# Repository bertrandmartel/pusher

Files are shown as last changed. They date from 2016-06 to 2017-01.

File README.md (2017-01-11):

# Pusher

 

Mechanical wall switch button pusher securely controlled via Bluetooth LE with RFduino module/LCD panel & via Android smartphone

Download Pusher from Google Play (https://play.google.com/store/apps/details?id=com.github.akinaru.roboticbuttonpusher)

demo

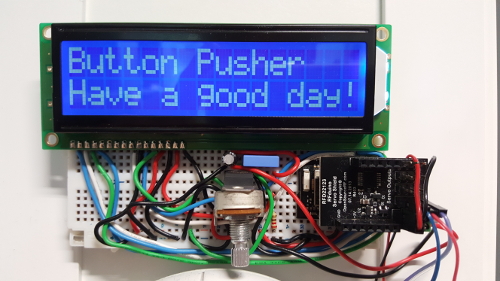
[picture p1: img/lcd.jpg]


***

Application layer association security  :

* AES 256 encryption
* user code for key exchange
* additional password protection

protected against MIM & Replay attack

pairing

## Project structure

* **/firmware** - microcontroller code written for RFduino
* **/android** - android application to control device
* **/hardware** - wiring diagram, schematics & BOM

## Build

### Get source code

```
git clone git@github.com:bertrandmartel/pusher.git
cd pusher
git submodule update --init --recursive
```

### Build Firmware

```
cd firmware
make
```

### Build Android App

```
cd android
./gradlew build
```

## [Firmware specifications](https://github.com/bertrandmartel/pusher/blob/master/firmware/README.md)

## [Hardware specifications](https://github.com/bertrandmartel/pusher/blob/master/hardware/README.md)

## External library

### Firmware

* rfduino software : https://github.com/RFduino/RFduino
* LiquidCrystal arduino library : https://github.com/arduino-libraries/LiquidCrystal
* rfduino-makefile : https://github.com/bertrandmartel/rfduino-makefile
* AES library by Brian Gladman

### Android application

* smart Android dot progress bar : https://github.com/silvestrpredko/DotProgressBarExample
* AES library by Brian Gladman
* appcompat-v7, design & recyclerview-v7

## License

```
Copyright (C) 2016  Bertrand Martel

This program is free software; you can redistribute it and/or
modify it under the terms of the GNU General Public License
as published by the Free Software Foundation; either version 3
of the License, or (at your option) any later version.

Pusher is distributed in the hope that it will be useful,
but WITHOUT ANY WARRANTY; without even the implied warranty of
MERCHANTABILITY or FITNESS FOR A PARTICULAR PURPOSE.  See the
GNU General Public License for more details.

You should have received a copy of the GNU General Public License
along with Pusher.  If not, see <http://www.gnu.org/licenses/>.
```

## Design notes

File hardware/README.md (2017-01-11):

## Hardware Specifications

Button pusher device is composed of :
* a mechanical part : servomotor + bracket + support
* an hardware part : rfduino uc + servo shield + LCD panel + voltage regulator

Check [Bill of Materials file](./BOM.xls) for a concise list of all hardware elements used in that project & links to some providers

### Hardware Parts

* [RFduino uc module](http://www.rfduino.com/product/rfd22102-rfduino-dip/index.html)

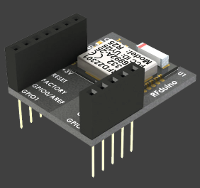
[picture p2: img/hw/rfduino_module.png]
rfduino


* [RFduino servo module](http://www.rfduino.com/product/rfd22123-servo-shield-for-rfduino/index.html)

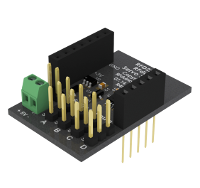
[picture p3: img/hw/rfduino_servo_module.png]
rfduino


* [3V3 NewHaven LCD panel](http://www.mouser.fr/Search/ProductDetail.aspx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)

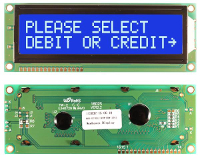
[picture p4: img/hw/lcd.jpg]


* [5V to 3V3 Voltage regulator LD1117V33](http://www.mouser.fr/ProductDetail/STMicroelectronics/LD1117V33/?qs=sGAEpiMZZMvHdo5hUx%252bJYl1lUmOd3DGr)

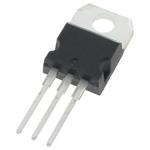
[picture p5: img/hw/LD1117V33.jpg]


* [Rfduino UART module](http://www.rfduino.com/product/rfd22121-usb-shield-for-rfduino/index.html) (for uploading/debgging purpose)

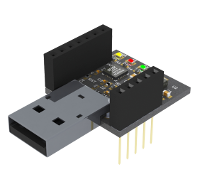
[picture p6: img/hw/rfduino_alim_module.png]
rfduino


### Prototype wiring 

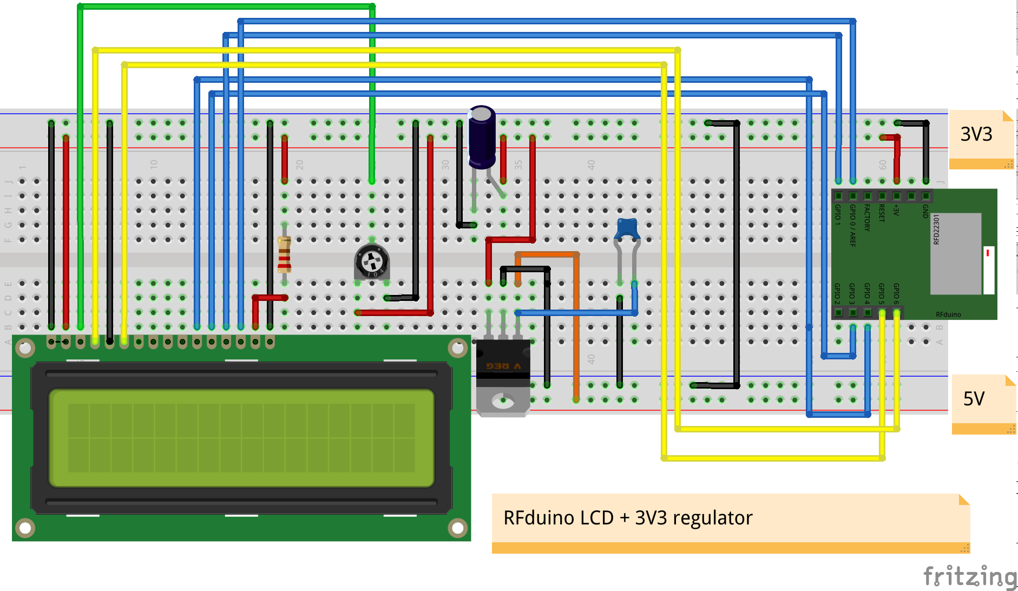
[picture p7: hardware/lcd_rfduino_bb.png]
wiring


### Mechanical Parts

This device is meant to push a wall switch of "Mosaic" type which is harder to push than a regular wall switch. To have enough force to push it, a servomotor with High Torque is used. HS-625MG is good for this task with a torque of 5.5 / 6.8 kg (http://www.imagesco.com/servo/motors/HS-625MG.html).

An aluminium sheet is used to support this servomotor : 

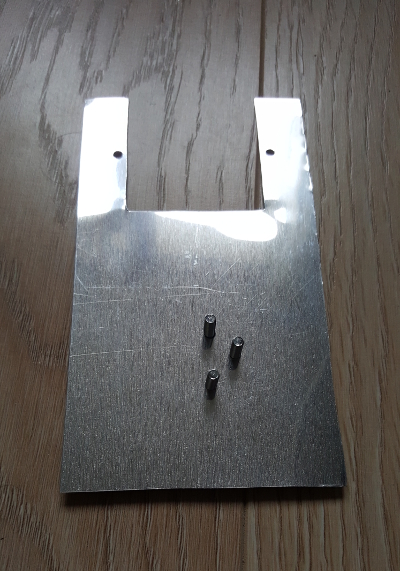
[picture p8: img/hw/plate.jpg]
aluminium_sheet


Servomotor is fixed to the bracket, the bracket is fixed to this plate :

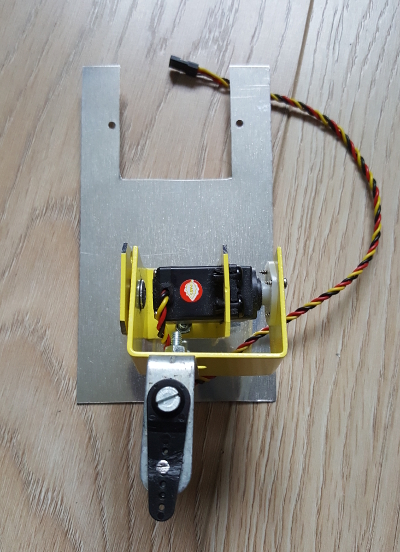
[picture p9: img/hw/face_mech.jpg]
bracket_servo


You can use 3.5mm or 4.mm screws with imagesco bracket (http://www.imagesco.com/catalog/servobot/SUB-01.pdf) :

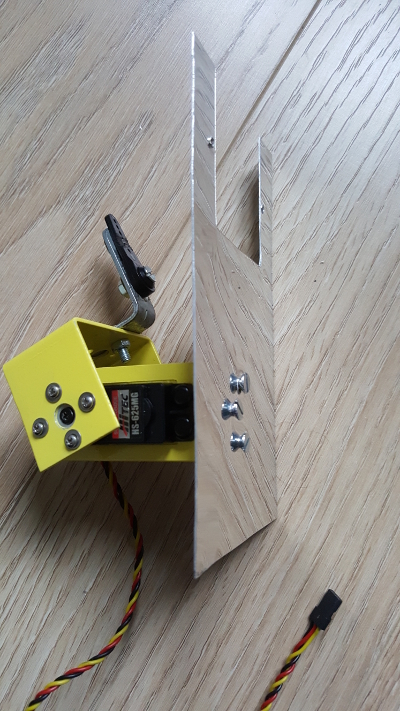
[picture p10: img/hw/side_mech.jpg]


The servomotor is then connected to Rfduino servo shield module that features an external 5V DC supply :

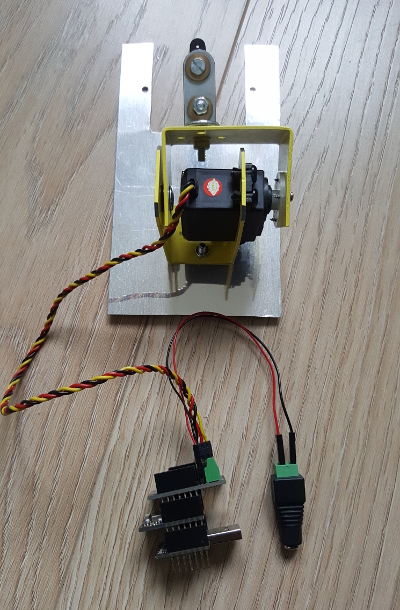
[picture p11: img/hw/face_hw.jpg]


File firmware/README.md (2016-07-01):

## Firmware Specifications

This wall switch pusher offers following features :
* push function
* LCD panel message
* secure association between Android smartphone & device via LCD panel
* persistent storage on the device to store associated device, security secrets such as key/iv, LCD panel message to be displayed
* all functionnalities except association are password protected

## Security features

This device uses AES 256 bit encyption based on the implementation by Brian Gladman (it used 8-bit byte operation only). The same implementation is used on both side, on Android & on RFduino uc.

Each smartphone Bluetooth controller will associate with the device generating a unique couple xor-key / serial number. This information is sent to the RFduino device and stored in persistent storage. The device will send back its AES key/iv. The whole association is protected by an AES key/iv generated from a random key the user must type on Android smartphone & generated by RFduino device. As a consequence, to associate with Rfduino device, a human must reproduce a visual information via the LCD panel.

All APIs are protected by a one-shot token generated by RFduino device. A GET_TOKEN API is used to retrieve this token from RFduino device. This token is encoded with Smartphone unique xor-key & AES encryption. This assure no replay attack is possible.

The critical APIs are secured by an additionnal password which must be changed when you setup the device for the first time. Default password is "admin". This password is encoded with the smartphone xor-key & encypted with AES.

## API parameters

* abbreviation
 * SN : serial number
 * pwd : password
 * token : random string (can be used only once)
 * AES : encyption with AES key stored on RFduino device
 * AES2 : encyption with AES key generated from user visual code (shared with user via LCD panel)
 * XOR : xor encryption with a xor-key user-specific (generated & exchanged at association)

|  name | code | input params |  output params  | LCD code |
|---|---|---|---|---|
| GET_TOKEN | 0x00 |  - | [token] |  no |
| ASSOCIATION_STATUS | 0x01 |  AES(SN + XOR([token])) | [status code] |  no |
| PUSH | 0x02 |  AES(SN + XOR(pwd + [token]))  | [status code] |  no |
| SET_PASSWORD | 0x03 |  AES(SN + XOR(pwd + [token]))  | [status code] |  yes | 
| ASSOCIATE | 0x04 |  - | [status code] |  yes | 
| SET_KEYS | 0x05 |  AES(SN + XOR(pwd + [token]))  | [status code] |  yes | 
| FAILURE | 0x06 |  - | - |  no | 
| ASSOCIATE_RESPONSE | 0x07 |  AES2(SN + XOR(pwd + [token])) | [status code] |  no | 
| RECEIVE_KEYS | 0x08 |  - | [status code] |  no | 
| SET_PASSWORD_RESPONSE | 0x09 |  AES2(SN + XOR(pwd + [token])) | [status code] |  no | 
| SET_KEYS_RESPONSE | 0x0A |  AES2(SN + XOR(pwd + [token])) | [status code] |  no | 
| DEASSOCIATE | 0x0B |  AES(SN + XOR(pwd + [token])) | [status code] |  no | 
| MESSAGE_TOP | 0x0C |  AES(SN + XOR(pwd + [token])) | [status code] |  no | 
| MESSAGE_BOTTOM | 0x0D |  AES(SN + XOR(pwd + [token])) | [status code] |  no |

## API description

|  name | description |
|---|---|
| GET_TOKEN |  get a token that can be used only once |
| ASSOCIATION_STATUS |  ask the device if the SN/XOR key pair sent is already associated |
| PUSH |  push wall switch |
| SET_PASSWORD |  change the password on the RFduino device, this will trigger a user code displayed on LCD |
| ASSOCIATE |  trigger association for the SN/XOR key pair sent, this will trigger a user code displayed on LCD |
| SET_KEYS |  change the AES key/iv on the RFduino device, this will trigger a user code displayed on LCD |
| FAILURE |  send a failure command |
| ASSOCIATE_RESPONSE |  send the association request encoded with the new AES2 key generated from user code |
| RECEIVE_KEYS |  request the keys from the RFduino device. This will only return keys if the association was performed just before |
| SET_PASSWORD_RESPONSE |  send the change-password request encoded with the new AES2 key generated from user code |
| SET_KEYS_RESPONSE |  send the change-keys request encoded with the new AES2 key generated from user code |
| DEASSOCIATE |  disassociate the SN/Xor key pair (delete from persistent storage as well) |
| MESSAGE_TOP |  change the top default message of the LCD screen |
| MESSAGE_BOTTOM |  change the bottom default message of the LCD screen |

## GATT protocol

* the above commands/APIs are sent via GATT characteristic `00002222-0000-1000-8000-00805f9b34fb`
* result is received via GATT characteristic `00002221-0000-1000-8000-00805f9b34fb` via notification

## Large data via GATT protocol

* The limit for GATT characteristic payload is 18 octet. The above commands load more than 18 octet, so payload is divided in bunch of 18 octet sent separatly. The first frame sent to Rfduino device is a frame containing the command code and the length of the payload. When the total payload is received from the device, it is processed directly and the response is returned via notification on characteristic `00002221-0000-1000-8000-00805f9b34fb`.

* The same protocol is used for receiving data from the Rfduino device. Data is split into bunch of 18 octet and sent until everything is received.

## Persistent storage

### Device configuration

Device configuration features a list of `device` structure featuring : 

| prototype | description |
|---|---|
| char device_id[8]  |  device serial |
| char xor_key[32] |  XOR key |

The maximum associated device number is 25 device (page size is 1024 octet)

### Global configuration

Global configuration features :

| prototype | description |
|---|---|
| char pass[4*16] |  encrypted password |
| uint16_t flag |  flag to check against default configuration |
| uint8_t device_num |  device_num for the number of smartphone device associated |
| char key[32] |  AES key |
| char iv[16] |  AES iv  |
| char top_message[28] | LCD panel top default message |
| char bottom_message[28] | LCD panel bottom default message |

### Memory page

* smartphone devices configuration is stored on page 250
* global configuration is stored on page 251

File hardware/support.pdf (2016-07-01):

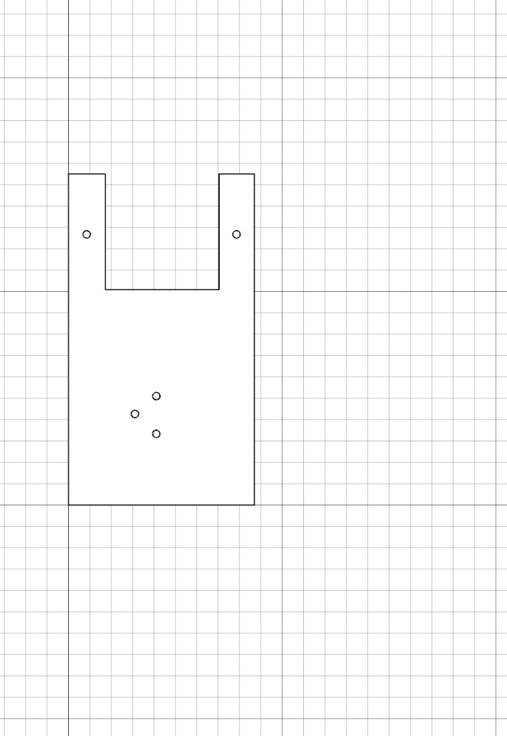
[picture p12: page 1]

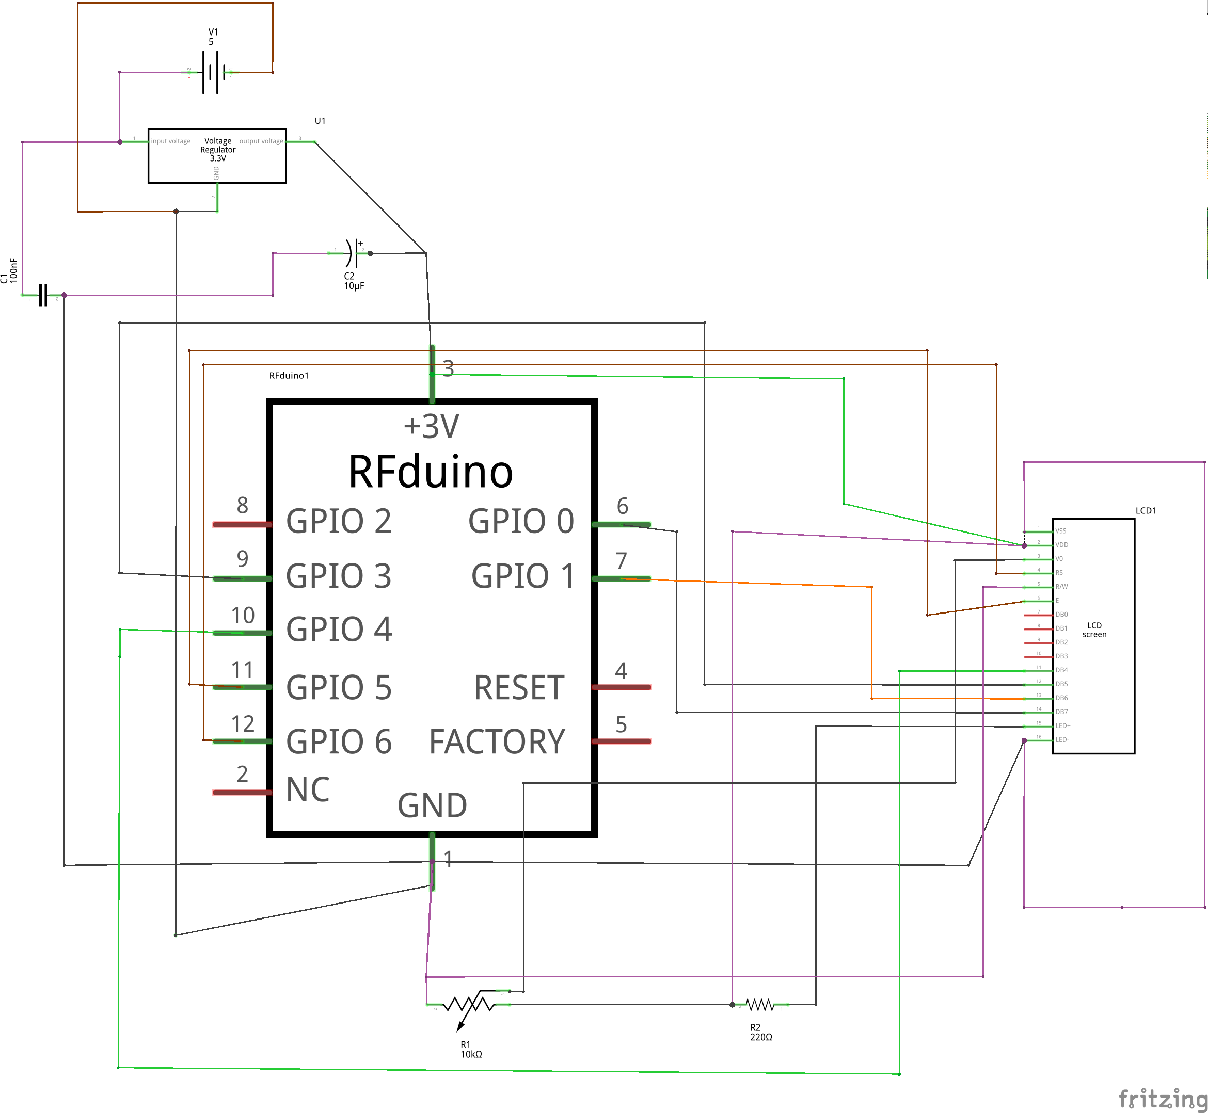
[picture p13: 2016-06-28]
hardware/lcd_rfduino_schem.png

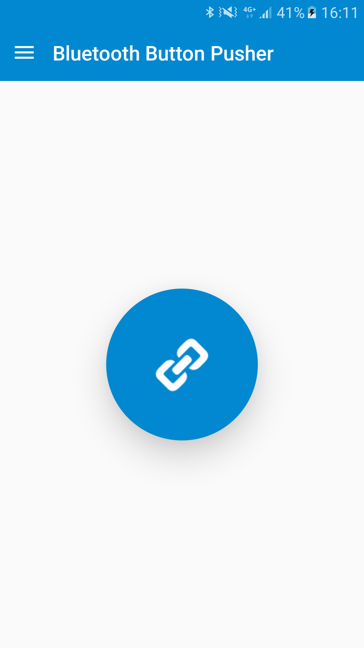
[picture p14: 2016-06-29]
img/screenshot1.png

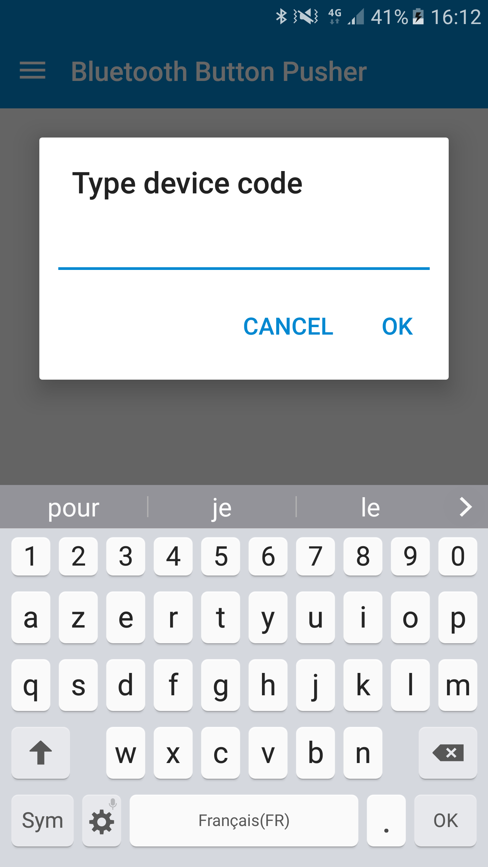
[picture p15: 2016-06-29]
img/screenshot2.png

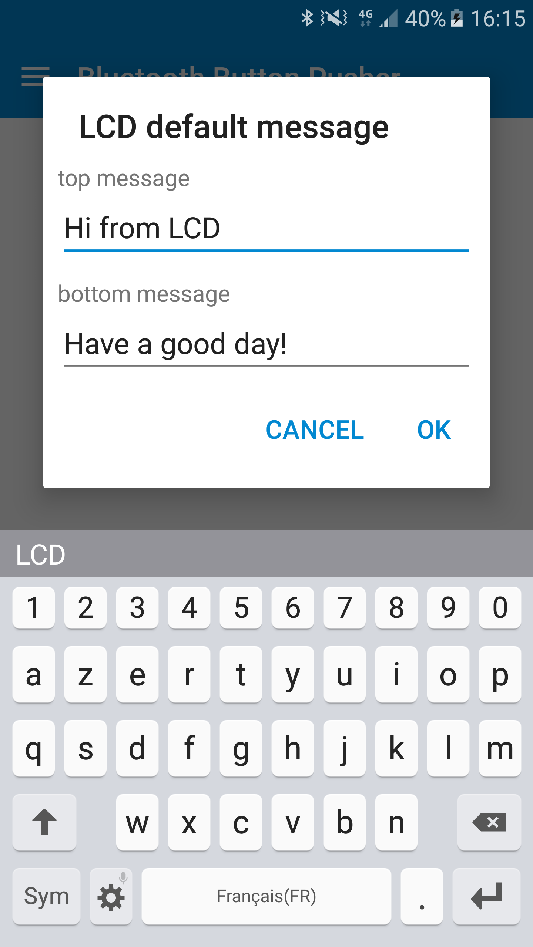
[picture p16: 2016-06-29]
img/screenshot6.png

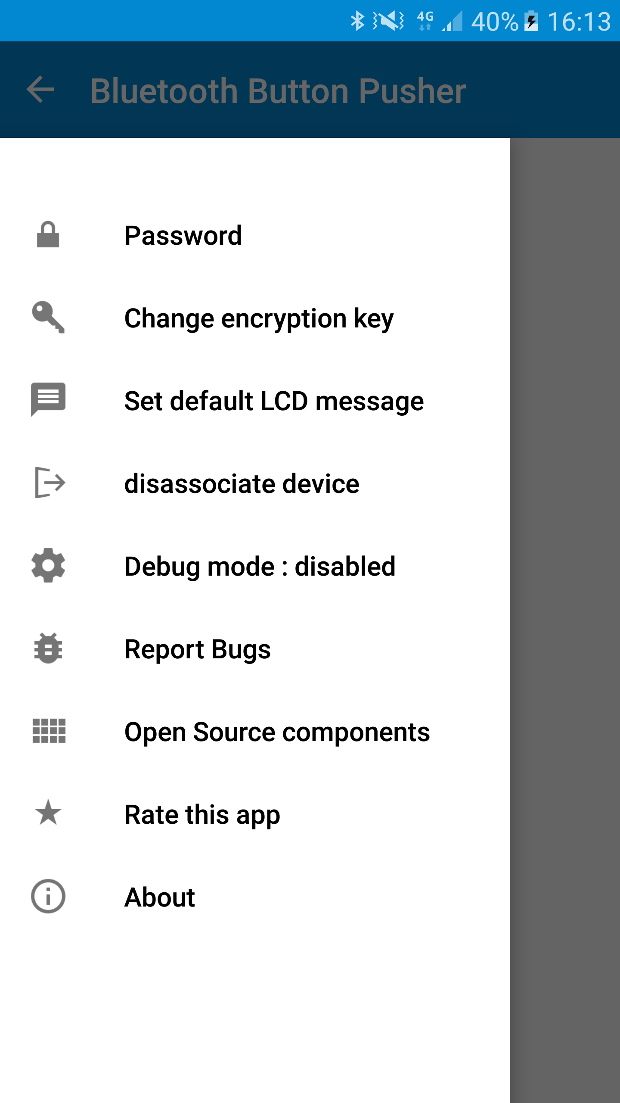
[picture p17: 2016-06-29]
img/screenshot3.png

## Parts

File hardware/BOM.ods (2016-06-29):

Mechanical Specifications
brand | model name | title | description | link | quantity | Price in $ (06/2016)
imagesco | SUB-01 | servomotor bracket | bracket used to initiate translation movement | http://www.imagesco.com/catalog/servobot/SUB-01.pdf | 1 | $12.50
 |  | aluminium sheet | sheet to be drilled to maintain the device with wall switch screws | http://www.castorama.fr/store/Tole-alu-brut-prod7220028.html | 1 | $7.58
 |  | screws 40mm diameter | to fix servomotor to aluminium sheet & servo arms to metal corner brace |  | 6
 |  | nuts 40mm | to fix servomotor to aluminium sheet & servo arms to metal corner brace |  | 5
 |  | washer 40mm | to fix servomotor to aluminium sheet & servo arms to metal corner brace |  | 6
Hitech | HS-625MG | servomotor | the servomotor to be chosen with high torque | http://www.imagesco.com/servo/motors/HS-625MG.html | 1 | $39.95
Hitech |  | Super-Duty Arms | small arms used to press the button from the metal corner : to prevent roughening wall switch surface | https://www.servocity.com/html/hitec_super-duty_horns.html#.V3PHmHV97CI | 1 | $10.95
 |  | Metal Corner Brace Angle Bracket Fasteners | mounting fixed to servo bracket used to press button | http://fr.aliexpress.com/item/1-3-5-x-1-3-5-Metal-Corner-Brace-Angle-Bracket-Fasteners-5-Pcs/32382146337.html | 1 | $5.67
Hardware Specifications
brand | model name | title | description | link | quantity | Price in $ (06/2016)
rfduino | RFD22102 | Rfduino DIP | Chip embedding cortex M0 + nRF81522 | http://eu.mouser.com/ProductDetail/RF-Digital-Wireless/RFD22102/ | 1 | $28.99
rfduino | RFD22121 | USB Shield for Rfduino | rfduino shield used to load code | http://www.mouser.fr/ProductDetail/RF-Digital/RFD22121/ | 1 | $28.99
rfduino | RFD22123 | Servo Shield for Rfduino | rfduino shield used to control up to 4 servomotors | http://www.mouser.fr/ProductDetail/RF-Digital/RFD22123/ | 1 | $18.94
 |  | switching power supply | power supply 5V 2A | https://www.adafruit.com/product/276 | 1 | $7.95
 |  | potentiometer 10K linear | potentiometer to control LCD contrast | https://www.adafruit.com/products/562 | 1 | $0.95
 |  | 220 ohm resistor | pull up resistor | https://www.adafruit.com/products/2780 | 1 | $0.75
 | LD1117V33 | voltage regulator | regulate 5V to 3.3V | https://www.adafruit.com/products/2165 | 1 | $1.25
 |  | capacitor 10uf | Protect capacitor for Vout | https://www.adafruit.com/products/2195 | 1 | $1.95
 |  | capacitor 100nf | Protect capacitor for Vin | https://www.adafruit.com/products/2195 | 1
 |  | DC jack converter | Female DC Power adapter - 2.1mm jack to screw terminal block | https://www.adafruit.com/products/368 | 1 | $2.00
 |  | LCD character display | 3.3V character display LCD | http://www.mouser.fr/Search/ProductDetail.aspx | 1 | $21.95
total estimated price for prototype |  | $190.37

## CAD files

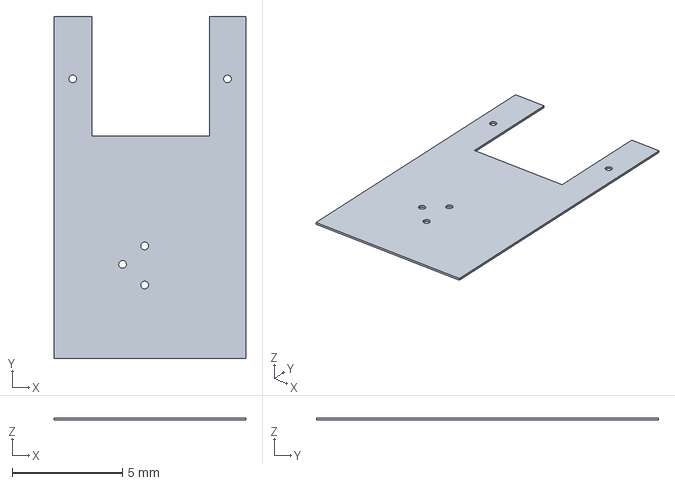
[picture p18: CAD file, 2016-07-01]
hardware/support.fcstd
8.70 x 15.5 x 0.1 mm

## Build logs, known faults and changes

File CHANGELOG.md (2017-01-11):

# Change Log

## [1.3](https://github.com/bertrandmartel/pusher/tree/1.3) (2016-07-05)
[Full Changelog](https://github.com/bertrandmartel/pusher/compare/1.2...1.3)

## [1.2](https://github.com/bertrandmartel/pusher/tree/1.2) (2016-07-01)
[Full Changelog](https://github.com/bertrandmartel/pusher/compare/1.1...1.2)

## [1.1](https://github.com/bertrandmartel/pusher/tree/1.1) (2016-07-01)
[Full Changelog](https://github.com/bertrandmartel/pusher/compare/1.0...1.1)

## [1.0](https://github.com/bertrandmartel/pusher/tree/1.0) (2016-06-29)

\* *This Change Log was automatically generated by [github_changelog_generator](https://github.com/skywinder/Github-Changelog-Generator)*

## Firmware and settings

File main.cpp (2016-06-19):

#include "Arduino.h"
#include <Servo.h>
#include <RFduinoBLE.h>
#include <string>
#include <LiquidCrystal.h>

#include <AES.h>

#define E(x,y) x = y,
enum STATE_ENUM {
#include "state.h"
};

#define E(x,y) #x,
static const char *STATE_STRING_ENUM[] = {
#include "state.h"
};

#define E(x,y) x = y,
enum COMMAND_ENUM {
#include "command.h"
};

#define E(x,y) #x,
static const char *COMMAND_STRING_ENUM[] = {
#include "command.h"
};

struct device
{
  char device_id[8];
  char xor_key[32];
};

#define LFSR_DEFAULT_VALUE 0xACE1u
#define MAX_ASSOCIATED_DEVICE 25
#define MESSAGE_DEFAULT "Have a good day!"
#define CODE_EXPIRING_TIME_SECONDS 30

device * device_ptr = new device[MAX_ASSOCIATED_DEVICE];
char token[16];

uint8_t state = STATE_NONE;
uint8_t state_count= 0;
uint8_t cmd = 0;
uint16_t data_length = 0;
bool use_local_keys = true;
uint16_t sending_index = 0;
bool code_expiring=false;
unsigned long code_expiring_time=0;

AES aes ;

byte default_key[32] = 
{
  0xF2, 0x1E, 0x07, 0x8C, 0x96, 0x99, 0x5E, 0xF7, 0xED, 0xF0, 0x91, 0x84, 0x06, 0x06, 0xF3, 0x94,
  0x59, 0x90, 0x66, 0x63, 0x81, 0xE9, 0x14, 0x3E, 0x7B, 0x02, 0x7E, 0x08, 0xB6, 0xC7, 0x06, 0x26
} ;

byte default_iv[16] = 
{
  0xC3, 0x78, 0x7E, 0x76, 0x31, 0x6D, 0x6B, 0x5B, 0xB8, 0x8E, 0xDA, 0x03, 0x82, 0xEB, 0x57, 0xBD
} ;

byte default_pass[64] = { 
  0x61, 0x64, 0x6d, 0x69, 0x6e, 0x00, 0x00, 0x00, 0x00, 0x00, 0x00, 0x00, 0x00, 0x00, 0x00, 0x00,
  0x00, 0x00, 0x00, 0x00, 0x00, 0x00, 0x00, 0x00, 0x00, 0x00, 0x00, 0x00, 0x00, 0x00, 0x00, 0x00,
  0x00, 0x00, 0x00, 0x00, 0x00, 0x00, 0x00, 0x00, 0x00, 0x00, 0x00, 0x00, 0x00, 0x00, 0x00, 0x00,
  0x00, 0x00, 0x00, 0x00, 0x00, 0x00, 0x00, 0x00, 0x00, 0x00, 0x00, 0x00, 0x00, 0x00, 0x00, 0x00,
};

byte external_key[32];
byte external_iv[16];

uint8_t* payload;
uint8_t* response;
uint8_t offset = 0;
uint16_t lfsr;

#define CONFIG_STORAGE 251
#define DEVICE_CONFIG_STORAGE 250

#define  str(x)   xstr(x)
#define  xstr(x)  #x

int interupt_pin = 31;

uint8_t myRandom8(){

  uint8_t __value;

  NRF_RNG->TASKS_START = 1; // Turn on the RNG.

  NRF_RNG->EVENTS_VALRDY = 0; // wait for a RNG value to be available

  while( NRF_RNG->EVENTS_VALRDY == 0 ){}
  __value = (uint8_t)NRF_RNG->VALUE; // read the RNG value

  NRF_RNG->TASKS_STOP = 1; // Turn off the RNG if we don't need it much.

  return(__value);
}

uint16_t myRandom16(){
  return(myRandom8() * myRandom8());
}

struct data_t
{
  char pass[4*N_BLOCK];
  uint16_t flag;
  uint8_t device_num;
  char key[32];
  char iv[16];
};

data_t config = { 
  "admin" ,
  0,
  0,
  {
  0xF2, 0x1E, 0x07, 0x8C, 0x96, 0x99, 0x5E, 0xF7, 0xED, 0xF0, 0x91, 0x84, 0x06, 0x06, 0xF3, 0x94,
  0x59, 0x90, 0x66, 0x63, 0x81, 0xE9, 0x14, 0x3E, 0x7B, 0x02, 0x7E, 0x08, 0xB6, 0xC7, 0x06, 0x26
},
  {
  0xC3, 0x78, 0x7E, 0x76, 0x31, 0x6D, 0x6B, 0x5B, 0xB8, 0x8E, 0xDA, 0x03, 0x82, 0xEB, 0x57, 0xBD
}
};

Servo s1;

bool add_device_pending = false;

data_t *in_flash = (data_t*)ADDRESS_OF_PAGE(CONFIG_STORAGE);

uint32_t *device_config = ADDRESS_OF_PAGE(DEVICE_CONFIG_STORAGE);

uint16_t bit;

LiquidCrystal lcd(6, 5, 4, 3, 1, 0);

uint16_t random()
{
  bit  = ((lfsr >> 0) ^ (lfsr >> 2) ^ (lfsr >> 3) ^ (lfsr >> 5) ) & 1;
  return lfsr =  (lfsr >> 1) | (bit << 15);
}

void write_host_config(device *item){

  int rc = flashWriteBlock(device_config, item, sizeof(device));
  device_config+=10;

    lcd.clear();
    lcd.print("write status : ");
    lcd.print(rc);
  
  #ifdef __PRINT_LOG__
    if (rc == 0){
      Serial.println("Success");
    }
    else if (rc == 1){
        Serial.println("Error - the flash page is reserved");
      }
    else if (rc == 2){
        Serial.println("Error - the flash page is used by the sketch");
      }
  #endif //__PRINT_LOG__
}

void save_config(bool default_config){

    #ifdef __PRINT_LOG__
      Serial.println("save_config");
    #endif //__PRINT_LOG__

    if (default_config){

      byte succ = aes.set_key (default_key, 256);

      int blocks = 4;
      byte cipher [4*N_BLOCK] ;
      byte iv [N_BLOCK];

      if (blocks == 1){
        succ = aes.encrypt(default_pass, cipher) ;
      }
      else {

        for (byte i = 0 ; i < N_BLOCK ; i++){
          iv[i] = default_iv[i] ;
        }
        succ = aes.cbc_encrypt(default_pass, cipher, blocks, iv) ;
      }

      for (byte i = 0; i < (4*N_BLOCK); i++){
        config.pass[i]=cipher[i];
      }

      #ifdef __PRINT_LOG__
        for (byte i = 0; i < (4*N_BLOCK); i++){
          Serial.print (cipher[i]>>4, HEX) ; Serial.print (cipher[i]&15, HEX) ; Serial.print (" ") ;
        }
        Serial.println();
      #endif //__PRINT_LOG__

      config.flag = 1;
      config.device_num=0;

      for (int i  =0;i< 32;i++){
        config.key[i]=default_key[i];
      }
      for (int i  =0;i< 16;i++){
        config.iv[i]=default_iv[i];
      }
    }
    
    while (!RFduinoBLE.radioActive);
    while (RFduinoBLE.radioActive);

    RFduinoBLE.end();

    flashPageErase(PAGE_FROM_ADDRESS(in_flash));

    while (RFduinoBLE_radioActive);

    flashWriteBlock(in_flash, &config, sizeof(config));

    if (add_device_pending){

      #ifdef __PRINT_LOG__
        Serial.println("in add_device_pending");
      #endif //__PRINT_LOG__

      if (config.device_num>0){

        #ifdef __PRINT_LOG__
          Serial.println("saving new associated device");
        #endif //__PRINT_LOG__

        write_host_config(&device_ptr[config.device_num-1]);
        //lcd.clear();
        //lcd.print("associated!");
      }
    }
}

void add_device(char * device_id,char * xor_key){

  #ifdef __PRINT_LOG__
    Serial.println("adding device in configuration");
  #endif //__PRINT_LOG__

  if (config.device_num<MAX_ASSOCIATED_DEVICE){

    #ifdef __PRINT_LOG__
      Serial.println(config.device_num);
    #endif //__PRINT_LOG__

    memcpy(device_ptr[config.device_num].device_id, device_id,8);
    memcpy(device_ptr[config.device_num].xor_key, xor_key,32);

    #ifdef __PRINT_LOG__
      Serial.println("add device to config");
    #endif //__PRINT_LOG__

    config.device_num++;

    add_device_pending=true;

    #ifdef __PRINT_LOG__
      Serial.println(config.device_num);
    #endif //__PRINT_LOG__

  }
  else{

    #ifdef __PRINT_LOG__
      Serial.println("error max device is reached");
    #endif //__PRINT_LOG__

  }
}

void load_fake_host_config(){

  for (int i = 0; i< MAX_ASSOCIATED_DEVICE;i++){

    if (i>=0){
      char buf[8];
      char xor_key[32];

      sprintf(buf, "d%d",i);
      sprintf(xor_key, "xor%d",i);

      strcpy(device_ptr[i].device_id, buf);
      strcpy(device_ptr[i].xor_key, xor_key);
    }
    else {
      char buf[8]={5, 21, 125, 245, 252, 14 ,86 ,59};
      char xor_key[32]={
        0x72, 0x6E , 0x35, 0x77, 0x6D, 0x64, 0x64, 0x64, 0x32, 0x62, 0x71, 0x31, 0x65, 0x64, 0x6B, 0x63, 0x62, 0x34, 0x68, 0x31, 0x76, 0x76, 0x73, 0x6B, 0x6F, 0x7A, 0x75, 0x71, 0x68, 0x33, 0x6A, 0x77
      };

      strcpy(device_ptr[i].device_id, buf);
      strcpy(device_ptr[i].xor_key, xor_key);
    }

    #ifdef __PRINT_LOG__
      Serial.print(i);
      Serial.print(" => ");
      Serial.print(device_ptr[i].device_id);
      Serial.print(" : ");
      Serial.println(device_ptr[i].xor_key);
    #endif //__PRINT_LOG__

  }
}

void print_all_config(){
  
  uint32_t *save_ptr = device_config;

  save_ptr = ADDRESS_OF_PAGE(DEVICE_CONFIG_STORAGE);

  device *item = 0;

  #ifdef __PRINT_LOG__
    Serial.println("-----------------------------");
    Serial.print("associated device list (size : ");
    Serial.print(config.device_num);
    Serial.println(") : ");
  #endif //__PRINT_LOG__
  
  for (int i = 0; i< config.device_num;i++){
    item = (device*)save_ptr;

    strcpy(device_ptr[i].device_id, item->device_id);
    strcpy(device_ptr[i].xor_key, item->xor_key);

    #ifdef __PRINT_LOG__
      for (int j = 0 ; j < 8;j++){
        Serial.print (device_ptr[i].device_id[j]>>4, HEX) ; Serial.print (device_ptr[i].device_id[j]&15, HEX) ; Serial.print (" ") ;
      }
      Serial.print(" | ");
      for (int j = 0 ; j < 32;j++){
        Serial.print (device_ptr[i].xor_key[j]>>4, HEX) ; Serial.print (device_ptr[i].xor_key[j]&15, HEX) ; Serial.print (" ") ;
      }
      Serial.println("");
    #endif //__PRINT_LOG__

    save_ptr+=10;
  }

  #ifdef __PRINT_LOG__
    Serial.println("-----------------------------");
  #endif //__PRINT_LOG__
}

void erase_host_config(){

  flashPageErase(PAGE_FROM_ADDRESS(device_config));

  for (int i = 0; i< MAX_ASSOCIATED_DEVICE;i++){
    strcpy(device_ptr[i].device_id, "");
    strcpy(device_ptr[i].xor_key, "");
  }
}

char* is_associated(char * device_id){

  Serial.println("in is_associated");
  for (int i  = 0; i  < 8;i++){
    char test[2];
    sprintf(test,"%02X",device_id[i]);
    Serial.print(test);
  }
  Serial.println("");

  for (int i = 0; i< MAX_ASSOCIATED_DEVICE;i++){

    if (memcmp(device_ptr[i].device_id,device_id,8)==0){
      return device_ptr[i].xor_key;
    }
  }
  return 0;
}

void remove_device(char * device_id){

  int index = 0;

  for (int i = 0; (i< MAX_ASSOCIATED_DEVICE);i++){

    if (memcmp(device_ptr[i].device_id,device_id,8)==0){
      index=i;
    }
  }
  if (index!=MAX_ASSOCIATED_DEVICE){
    for (int i = index;i<MAX_ASSOCIATED_DEVICE-1;i++){
      strcpy(device_ptr[i].device_id, device_ptr[i+1].device_id);
      strcpy(device_ptr[i].xor_key  , device_ptr[i+1].xor_key);
    }
  }
  config.device_num--;
  add_device_pending=true;
  print_all_config();
}

void write(){
 
  in_flash = (data_t*)ADDRESS_OF_PAGE(CONFIG_STORAGE);

  if (in_flash->flag != 1){

    #ifdef __PRINT_LOG__
      Serial.println("writing default configuration");
    #endif //__PRINT_LOG__

    save_config(true);
    
    erase_host_config();
    //load_fake_host_config();

    RFduinoBLE.begin();
  }
  else {

    #ifdef __PRINT_LOG__
      Serial.println("getting default configuration");
    #endif //__PRINT_LOG__

    for (byte i = 0; i < (4*N_BLOCK); i++){
      config.pass[i]=in_flash->pass[i];
    }
    
    config.flag=1;
    config.device_num=in_flash->device_num;

    for (int i = 0; i < 32;i++){
      config.key[i]=in_flash->key[i];
    }

    for (int i = 0; i < 16;i++){
      config.iv[i]=in_flash->iv[i];
    }

    #ifdef __PRINT_LOG__
      Serial.print("encrypted password : ");
      for (byte i = 0; i < (4*N_BLOCK); i++){
        Serial.print ( config.pass[i]>>4, HEX) ; Serial.print ( config.pass[i]&15, HEX) ; Serial.print (" ") ;
      }
      Serial.println();
    #endif //__PRINT_LOG__
  }

  print_all_config();
}

void print_lcd_message(char * header,char * message){
  lcd.clear();
  lcd.setCursor(0,0);
  lcd.print(header);
  lcd.setCursor(0,1);
  lcd.print(message);
}

void setup() {

  #ifdef __PRINT_LOG__
   Serial.begin(9600);
  #endif //__PRINT_LOG__
  
  lcd.begin(16, 2);

  print_lcd_message(MESSAGE_DEFAULT,"");

  lfsr = myRandom16();

  RFduinoBLE.advertisementData = "open LAB";

  RFduinoBLE.begin();

  //prekey(256,4);
  write();
}

bool interrupting(){

  if(RFduino_pinWoke(interupt_pin)){

    RFduino_resetPinWake(interupt_pin);

    return HIGH;
  }
  return LOW;
}

void loop() {
 
  //RFduinoBLE_ULPDelay(INFINITE); 
  delay(500);
  
  if(interrupting()){

    #ifdef __PRINT_LOG__
      Serial.println("interrupting");
    #endif //__PRINT_LOG__

    save_config(false);
    add_device_pending=false;
    RFduinoBLE.begin();
    //print_lcd_message(MESSAGE_DEFAULT,"");
  }
  
  if (code_expiring){

    int rem = code_expiring_time-millis();

    if (code_expiring_time!=0 && rem<=0){
      Serial.println("code has expired");
      code_expiring_time=0;
      code_expiring=false;
      memset(token, 0, 8);
      memset(external_iv, 0, 16);
      memset(external_key, 0, 32);
      lcd.clear();
      lcd.print(MESSAGE_DEFAULT);
    }
  }
}

void interrupt(){

  #ifdef __PRINT_LOG__
    Serial.println("interrupt()");
  #endif //__PRINT_LOG__

  NRF_GPIO->PIN_CNF[interupt_pin] = (GPIO_PIN_CNF_PULL_Pullup<<GPIO_PIN_CNF_PULL_Pos);

  RFduino_pinWake(interupt_pin,HIGH);

  NRF_GPIO->PIN_CNF[interupt_pin] = (GPIO_PIN_CNF_PULL_Pulldown<<GPIO_PIN_CNF_PULL_Pos);
}

void motor_process()
{
  for(int angle = 0; angle < 175; angle++)
  {
    s1.write(angle);
    delay(5);
  }
  delay(500);
  
  for(int angle = 174; angle >0;angle--)
  {
    s1.write(angle);
    delay(5);
  }
}

void RFduinoBLE_onDisconnect(){

  #ifdef __PRINT_LOG__
    Serial.println("onDisconnect");
  #endif //__PRINT_LOG__
  memset(token, 0, 8);
  memset(external_iv, 0, 16);
  memset(external_key, 0, 32);
  code_expiring=false;
  code_expiring_time=0;
  use_local_keys=true;
  free(response);
  response=0;
  free(payload);
  payload=0;
  interrupt();
}

void sendCommandStatus(int cmd, bool status){

  char req[2]={0};
  uint8_t status_d = 1;
  if (status){
    status_d=0;
  }
  sprintf(req, "%c:%c", cmd,status_d);
  RFduinoBLE.send(req,10);
}

void sendCommandFailure(){
  char req[1]={0};
  sprintf(req, "%c", COMMAND_FAILURE);

  #ifdef __PRINT_LOG__
    Serial.println("send association failure");
  #endif //__PRINT_LOG__

  RFduinoBLE.send(req,2);
}

void processEncryptedResponse(byte * check){

  #ifdef __PRINT_LOG__
    Serial.println(COMMAND_STRING_ENUM[cmd]);
  #endif //__PRINT_LOG__

  if (strlen(token) == 0){
    switch(cmd){
      case COMMAND_ASSOCIATE_RESPONSE:
      {
        sendCommandStatus(COMMAND_ASSOCIATE,false);
        return;
      }
      case COMMAND_SET_PASSWORD_RESPONSE:
      {
        sendCommandStatus(COMMAND_SET_PASSWORD,false);
        return;
      }
      case COMMAND_SET_KEYS_RESPONSE:
      {
        sendCommandStatus(COMMAND_SET_KEY,false);
        return;
      }
    }
    return;
  }
}

void generate_key(byte * code,byte * key){
  
  uint16_t lfsr;

  lfsr = (code[0]<<8) + code[1];

  uint8_t j = 2;
  uint8_t k = 0;

  for (int i = 0; i  < 16;i++){

    if (i!=0 && ((i%4)==0)){

      lfsr = (code[j]<<8) + code[j+1];
      j+=2;
    }
    uint16_t bit  = ((lfsr >> 0) ^ (lfsr >> 2) ^ (lfsr >> 3) ^ (lfsr >> 5) ) & 1;
    lfsr =  (lfsr >> 1) | (bit << 15);

    key[k] = (lfsr & 0xFF00)>>8;
    k++;
    key[k] = (lfsr & 0x00FF)>>0;
    k++;
  }
}

void generate_iv(byte * code, byte * iv){

  for (int i = 0; i  < 8;i++){
    iv[i] = code[i];
  }

  uint16_t lfsr;
  uint8_t k = 0;
  uint8_t j = 0;

  for (int i = 0; i  < 4;i++){
    lfsr = (code[j]<<8) + code[j+1];
    j+=2;
    uint16_t bit  = ((lfsr >> 0) ^ (lfsr >> 2) ^ (lfsr >> 3) ^ (lfsr >> 5) ) & 1;
    lfsr =  (lfsr >> 1) | (bit << 15);
    iv[k+8] = (lfsr & 0xFF00)>>8;
    k++;
    iv[k+8] = (lfsr & 0x00FF)>>0;
    k++;
  }
}

void generateRandomKeys(){

  //generate a key from 8 octet random
  uint16_t lfsr1 = random();
  uint16_t lfsr2 = random();
  uint16_t lfsr3 = random();
  uint16_t lfsr4 = random();

  char tokenStr[16];
  sprintf(tokenStr, "%04x%04x%04x%04x", lfsr1, lfsr2,lfsr3,lfsr4);

  #ifdef __PRINT_LOG__
    Serial.println(tokenStr);
  #endif //__PRINT_LOG__

  byte code[8];
  code[0]=((lfsr1 & 0xFF00)>>8);
  code[1]=((lfsr1 & 0x00FF)>>0);
  code[2]=((lfsr2 & 0xFF00)>>8);
  code[3]=((lfsr2 & 0x00FF)>>0);
  code[4]=((lfsr3 & 0xFF00)>>8);
  code[5]=((lfsr3 & 0x00FF)>>0);
  code[6]=((lfsr4 & 0xFF00)>>8);
  code[7]=((lfsr4 & 0x00FF)>>0);

  generate_key(code,external_key);
  generate_iv(code,external_iv);
  code_expiring_time = millis()+CODE_EXPIRING_TIME_SECONDS*1000;
  code_expiring=true;

  #ifdef __PRINT_LOG__
    Serial.println("code : ");
    for (int i = 0 ; i < 8;i++){
      Serial.print (code[i]>>4, HEX) ; Serial.print (code[i]&15, HEX) ; Serial.print (" ") ;
      if ((i!=0) && (i%15==0)){
        Serial.println("");
      }
    }
    Serial.println("");

    Serial.println("key2 : ");
    for (int i = 0 ; i < 32;i++){
      Serial.print (external_key[i]>>4, HEX) ; Serial.print (external_key[i]&15, HEX) ; Serial.print (" ") ;
      if ((i!=0) && (i%15==0)){
        Serial.println("");
      }
    }
    Serial.println("");

    Serial.println("iv2 : ");
    for (int i = 0 ; i < 16;i++){
      Serial.print (external_iv[i]>>4, HEX) ; Serial.print (external_iv[i]&15, HEX) ; Serial.print (" ") ;
      if ((i!=0) && (i%15==0)){
        Serial.println("");
      }
    }
    Serial.println("");
  #endif //__PRINT_LOG__

  print_lcd_message("pairing code :",tokenStr);
}

void processEncryptedFrame(byte * check){

  if (strlen(token) == 0){

    #ifdef __PRINT_LOG__
      Serial.println("no token");
    #endif //__PRINT_LOG__

    print_lcd_message("command failure:","no token sent");

    sendCommandStatus(COMMAND_PUSH,false);
    return;
  }

  char device_id[8];

  for (int i = 0; i< 8;i++){
    device_id[i] = check[i];
  }

  char * xor_key = is_associated(device_id);

  if (xor_key!=0){

    #ifdef __PRINT_LOG__
      Serial.println("device associated, continuing ...");
    #endif //__PRINT_LOG__

    char xored_hash[28];
    for (int i = 8;i < 36;i++){
      xored_hash[i-8] = check[i];
    }

    char xor_decoded[28];

    
    for (int j = 0 ;j  < 28;j++){
      xor_decoded[j]=xored_hash[j]^xor_key[j];
    }

    #ifdef __PRINT_LOG__
      Serial.println("xor decoded : ");
      for (int i = 0; i < 8;i++){
        Serial.print((int)xor_decoded[i]);
        Serial.print("=>");
        Serial.print((int)token[i]);
        Serial.print(" ");
      }
      Serial.println("");
    #endif //__PRINT_LOG__

    if (memcmp(token,xor_decoded,8)==0){

      memset(token, 0, 8);

      char sent_pass[64];
      char pass_temp[64];

      for (int i = 8;i<28;i++){
        sent_pass[i-8] = xor_decoded[i];
      }
      for (int i = 20;i<64;i++){
        sent_pass[i]=0;
      }

      //decrypt current pass
      byte pass[64];

      byte iv[16];
      byte cipher[64];
      byte key[32];
      for (int i = 0; i < 32;i++){
        key[i]=config.key[i];
      }
      byte succ = aes.set_key (key, 256);

      for (byte i = 0 ; i < 16 ; i++){
        iv[i] = config.iv[i] ;
      }
      for (byte i = 0 ; i< 64;i++){
        cipher[i] = config.pass[i];
      }
      //decrypt
      succ = aes.cbc_decrypt(cipher, pass, 4, iv) ;
      
      for (int i  =0; i  < 64;i++){
        pass_temp[i]=pass[i];
      }

      if (memcmp(sent_pass,pass_temp,64)==0){

        switch (cmd){
          case COMMAND_PUSH:
          {
            #ifdef __PRINT_LOG__
              Serial.println("push success");
            #endif //__PRINT_LOG__

            print_lcd_message("command status :","push success");

            sendCommandStatus(COMMAND_PUSH,true);
            s1.attach(2);
            motor_process();
            s1.detach();
            break;
          }
          case COMMAND_SET_PASSWORD:
          {
            generateRandomKeys();

            #ifdef __PRINT_LOG__
              Serial.println("set password request success");
            #endif //__PRINT_LOG__

            use_local_keys= false;
            char buf[3]={0};
            sprintf(buf, "%c:%c", COMMAND_SET_PASSWORD, 2);
            RFduinoBLE.send(buf,3);
            break;
          }
          case COMMAND_SET_KEY:
          {
            generateRandomKeys();

            #ifdef __PRINT_LOG__
              Serial.println("set keys request success");
            #endif //__PRINT_LOG__

            use_local_keys= false;
            char buf[3]={0};
            sprintf(buf, "%c:%c", COMMAND_SET_KEY, 2);
            RFduinoBLE.send(buf,3);
            break;
          }
          case COMMAND_DISASSOCIATION:
          {
            #ifdef __PRINT_LOG__
              Serial.println("disassociation success");
            #endif //__PRINT_LOG__

            print_lcd_message("command status :","unpairing OK");

            remove_device(device_id);
            char buf[3]={0};
            sprintf(buf, "%c:%c", COMMAND_DISASSOCIATION, 0);
            RFduinoBLE.send(buf,3);
          }
        }
      }
      else{

        lcd.clear();
        lcd.print(succ);
        //print_lcd_message(sent_pass,pass_temp);

        #ifdef __PRINT_LOG__
          Serial.println("cmd failure : bad pass");
        #endif //__PRINT_LOG__

        sendCommandStatus(cmd,false);
      } 
    }
    else{

      print_lcd_message("command failure:","bad token");

      memset(token, 0, 8);

      #ifdef __PRINT_LOG__
        Serial.println("cmd failure : bad token");
      #endif //__PRINT_LOG__

      sendCommandStatus(cmd,false);
    }
  }
  else{

    print_lcd_message("command failure:","not associated");

    #ifdef __PRINT_LOG__
      Serial.println("device not associated, aborting ...");
    #endif //__PRINT_LOG__

    sendCommandStatus(cmd,false);
  }
}
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
int main() {

  init();
  setup();
  while(1)
    loop();
  return 0;
}

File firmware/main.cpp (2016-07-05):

/**********************************************************************************
 * This file is part of Pusher.                                                    *
 * <p/>                                                                            *
 * Copyright (C) 2016  Bertrand Martel                                             *
 * <p/>                                                                            *
 * Pusher is free software: you can redistribute it and/or modify                  *
 * it under the terms of the GNU General Public License as published by            *
 * the Free Software Foundation, either version 3 of the License, or               *
 * (at your option) any later version.                                             *
 * <p/>                                                                            *
 * Pusher is distributed in the hope that it will be useful,                       *
 * but WITHOUT ANY WARRANTY; without even the implied warranty of                  *
 * MERCHANTABILITY or FITNESS FOR A PARTICULAR PURPOSE.  See the                   *
 * GNU General Public License for more details.                                    *
 * <p/>                                                                            *
 * You should have received a copy of the GNU General Public License               *
 * along with Pusher. If not, see <http://www.gnu.org/licenses/>.                  *
 */
#include "Arduino.h"
#include <RFduinoBLE.h>
#include <lcd/LiquidCrystal.h>
#include <aes/AES.h>
#include "config/config.h"
#include "crypto/crypto.h"
#include "constants.h"
#include "process/process.h"
#include "lcd/LcdPrinter.h"

Crypto crypto;
Config config;
AES aes;
LcdPrinter lcd_printer;

Process process;
LiquidCrystal lcd(6, 5, 4, 3, 1, 0);

void setup() {

  #ifdef __PRINT_LOG__
  Serial.begin(9600);
  #endif //__PRINT_LOG__
  
  lcd.begin(16, 2);

  config.init(&lcd, &aes);
  lcd_printer.init(&lcd,&config);
  process.init(&lcd_printer,&aes,&config,&crypto);

  RFduinoBLE.advertisementData = ADVERTISMENT_DATA;

  RFduinoBLE.begin();

  config.restore();

  lcd_printer.print_default_message();
}

bool interrupting(){

  if(RFduino_pinWoke(INTERRUPT_PIN)){

    RFduino_resetPinWake(INTERRUPT_PIN);

    return HIGH;
  }
  return LOW;
}

void loop() {

  delay(500);
  
  if(interrupting()){

    #ifdef __PRINT_LOG__
      Serial.println("interrupting");
    #endif //__PRINT_LOG__
      

    if (config.is_save_conf() || config.is_device_pending()){
      config.save_config(false);
      RFduinoBLE.begin();
    }
    
    config.set_save_conf(false);
    config.set_device_pending(false);


    lcd_printer.print_default_message();
  }
  
  if (process.is_code_expiring()){

    int rem = process.get_code_expiring_time()-millis();

    if (process.get_code_expiring_time()!=0 && rem<=0){
      
      #ifdef __PRINT_LOG__
      Serial.println("code has expired");
      #endif //__PRINT_LOG__

      process.clear();

      lcd_printer.print_default_message();
    }
  }
}

void interrupt(){

  #ifdef __PRINT_LOG__
  Serial.println("interrupt()");
  #endif //__PRINT_LOG__

  NRF_GPIO->PIN_CNF[INTERRUPT_PIN] = (GPIO_PIN_CNF_PULL_Pullup<<GPIO_PIN_CNF_PULL_Pos);

  RFduino_pinWake(INTERRUPT_PIN,HIGH);

  NRF_GPIO->PIN_CNF[INTERRUPT_PIN] = (GPIO_PIN_CNF_PULL_Pulldown<<GPIO_PIN_CNF_PULL_Pos);
}

void RFduinoBLE_onConnect()
{
  lcd_printer.print_lcd_message("A device is","connected");
}

void RFduinoBLE_onDisconnect(){

  #ifdef __PRINT_LOG__
  Serial.println("onDisconnect");
  #endif //__PRINT_LOG__

  process.clear();

  interrupt();
}

void RFduinoBLE_onReceive(char *data, int len){
  
  process.process_state(data,len);

}

int main() {

  init();
  setup();
  while(1)
    loop();
  return 0;
}

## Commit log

2016-06-01 create repo button pusher
2016-06-01 add menu items : device name, password, debug mode
2016-06-02 complete data flow + success/failure animation
2016-06-03 fix bluetooth state + device disconnection
2016-06-03 fix device disconnection + implement widget
2016-06-08 configure command flow + device memory mapping
2016-06-09 store device_id /xor_key pair in flash storage on association success
2016-06-13 set password on device implementation
2016-06-19 fix device configuration persistent storage
    [main.cpp]
2016-06-19 remove device name configuration in android app
2016-06-27 delay for success/error message
    [process.cpp]
2016-06-27 hardware part : fritzing
    [lcd_rfduino.fzz]
2016-06-28 dont set the default config on reboot
    [config.cpp]
2016-06-28 fritzing schematics
    [lcd_rfduino.fzz]
2016-06-28 update fritzing
    [lcd_rfduino.fzz]
2016-06-29 remove device if already existing in config
2016-06-29 add BOM
    [BOM.ods, BOM.xls]
2016-06-29 fix add/remove device configuration bug
    [config.cpp, process.cpp]
2016-07-01 servo support plate on freecad
    [support.fcstd]
2017-01-17 init servo value - increase speed - configure servo pin
